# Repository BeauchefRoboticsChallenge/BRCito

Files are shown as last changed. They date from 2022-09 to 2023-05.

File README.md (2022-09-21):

# BRCito 2022

[][cc-by-nc-sa]

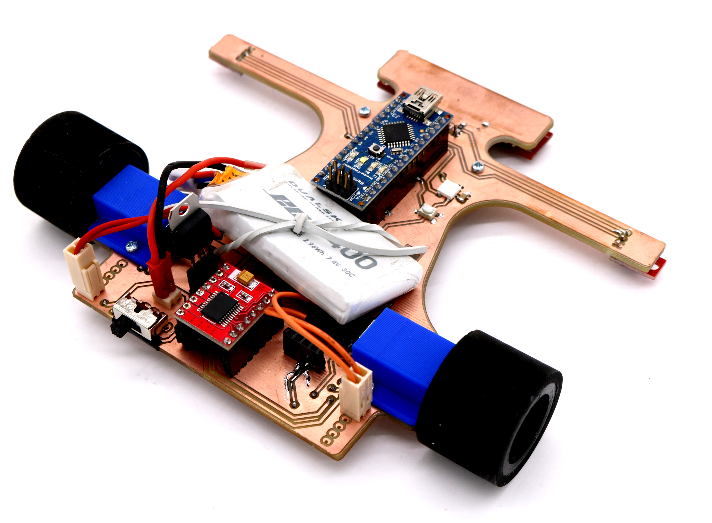
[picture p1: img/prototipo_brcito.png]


Robot velocista sigue-líneas desarrollado para BRC 2022.

El objetivo de este robot es servir de referencia y plataforma para apoyar la formación de los competidores. Está desarrollado en base a las tecnologías disponibles en un FabLab (impresión 3D, fresado de PCBs, Arduino) y comprende las componentes más básicas para funcionar de acuerdo a las reglas de la competencia.

Para poder entregar robots a los colegios participantes de la liga **Sub18** recibimos auspicio de [PCBWay](https://www.pcbway.com/) quienes nos otorgaron las placas electrónicas.

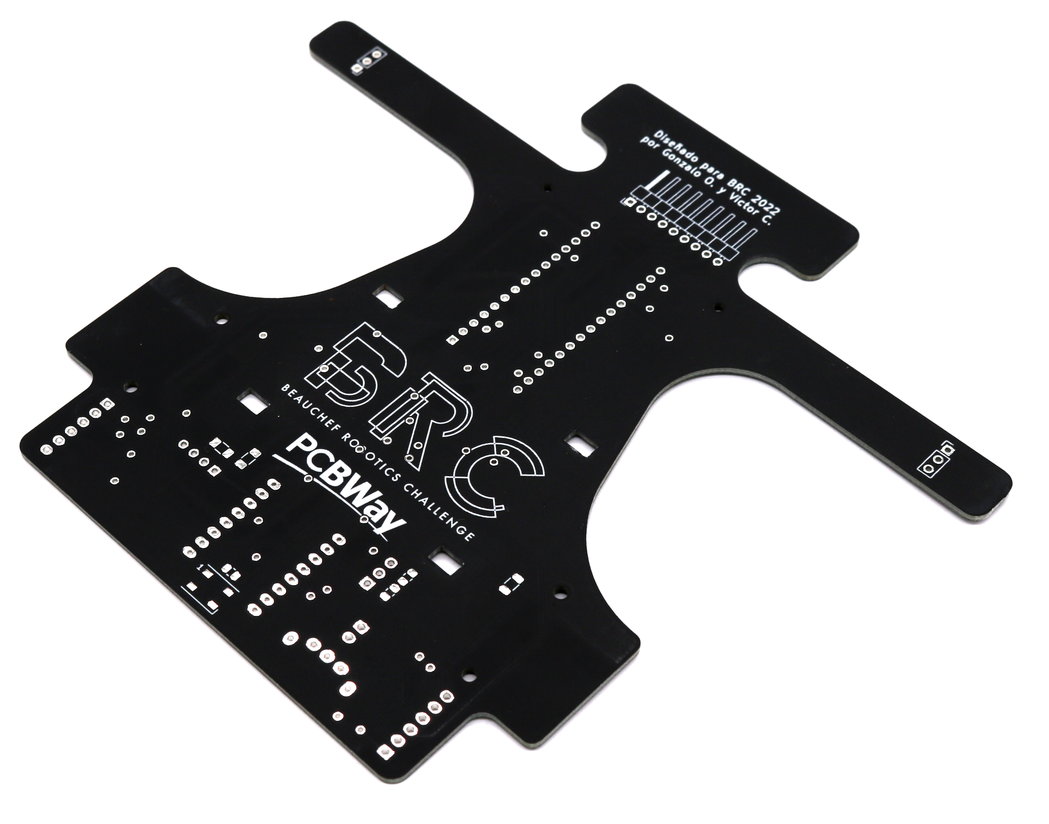
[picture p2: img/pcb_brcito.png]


## Diseño

### Antecedentes

Las funciones principales requeridas por el robot son:

- Distinguir una línea blanca en un fondo blanco
- Moverse lo más rápido posible, sin salirse de la pista

Para cumplir estas funciones, el robot requiere una construcción óptima en cuanto al tamaño/peso y las prestaciones de sus componentes que cumplirán estas funcionalidades. El diseño del robot puede seguir diferentes configuraciones (arreglos de sensores, motores, baterías, etc), dependiendo del tipo de control que se vaya a utilizar. Otras funciones secundarias corresponden a la interacción con el usuario (encender/apagar, activar, indicar acciones), así como cualquier otra que se desee agregar (como comunicación inalámbrica para el debugging).

En el contexto de la competencia, existirán marcadores a los costados del circuito que indicarán hitos como curvas, inicio y fin de la pista. También se fija el tamaño máximo como 25x25x20 centímetros (largo, ancho y alto) y que las ruedas no pueden contener elementos adherentes que dañen la pista.

### BRCito Negro PCBWay

El robot sigue líneas es controlador por un Arduino Nano. Las conexiones del Arduino con los sensores, necesarias para realizar su programación se pueden ver en la tabla

#### Pinout electrónico
| Pin Arduino | Descripción | Componente | Pin componente
| :--- | :--- | :--- | :-----  |
| A2 | Sensor Frontal 1 | Arreglo sensores QTR-8A | 6
| A3 | Sensor Frontal 2 | Arreglo sensores QTR-8A |5
| A4 | Sensor Frontal 3 | Arreglo sensores QTR-8A |4
| A5 | Sensor Frontal 4 | Arreglo sensores QTR-8A |3
| A6 | Sensor Frontal 5 | Arreglo sensores QTR-8A |2
| A7 | Sensor Frontal 6 | Arreglo sensores QTR-8A |1
| 6 | Rueda izquierda PWM | Driver motor TB6612FNG | PWMA
| 13 | Rueda izquierda A | Driver motor TB6612FNG  | AI1 |
| 10 | Rueda izquierda B | Driver motor TB6612FNG | AI2  |
| 5 | Rueda derecha PWM | Driver motor TB6612FNG | PWMB |
| 11 | Rueda derecha A | Driver motor TB6612FNG  | BI1 |
| 12 | Rueda derecha B | Driver motor TB6612FNG | BI2  |
| A1 | Sensor derecho | Sensor QTR-1A | out
| A0 | Sensor izquierdo | Sensor QTR-1A | out
| 9 | Leds RGB | Led RGB | din led
| 7 | Pulsador | Pulsador | pin pulsador

### Librerías de Kicad

En la carpeta [pcb/libs/](pcb/libs/) se encuentran las librerías de símbolos y footprints diseñados para los componentes que no existen en las librerías estandar de KiCad.

**Librería de símbolos**
* TB6612FNG_breakout

**Librería de footprints**
* QTR-8
* SPST Slide Switch (interruptor)
* TB6612FNG Breakout

## Librerías de Arduino

Para comunicarse con los leds WS2812b se puede utilizar la librería [Adafruit Neopixel](https://github.com/adafruit/Adafruit_NeoPixel).

Para los sensores infrarrojos QTR se puede utilizar la librería [QTR Sensors](https://github.com/pololu/qtr-sensors-arduino).

## Licencia
[][cc-by-nc-sa]

Este trabajo esta publicado bajo la licencia [Creative Commons Attribution-NonCommercial-ShareAlike 4.0 International
License][cc-by-nc-sa].

Si deseas utilizar nuestro robot en tus proyectos o si te interesa vender las placas, contáctanos y conversemos :)

[cc-by-nc-sa]: https://creativecommons.org/licenses/by-nc-sa/4.0/
[cc-by-nc-sa-image]: https://i.creativecommons.org/l/by-nc-sa/4.0/88x31.png
[cc-by-nc-sa-shield]: https://img.shields.io/badge/License-CC%20BY%20NC%20SA%204.0-lightgrey.svg

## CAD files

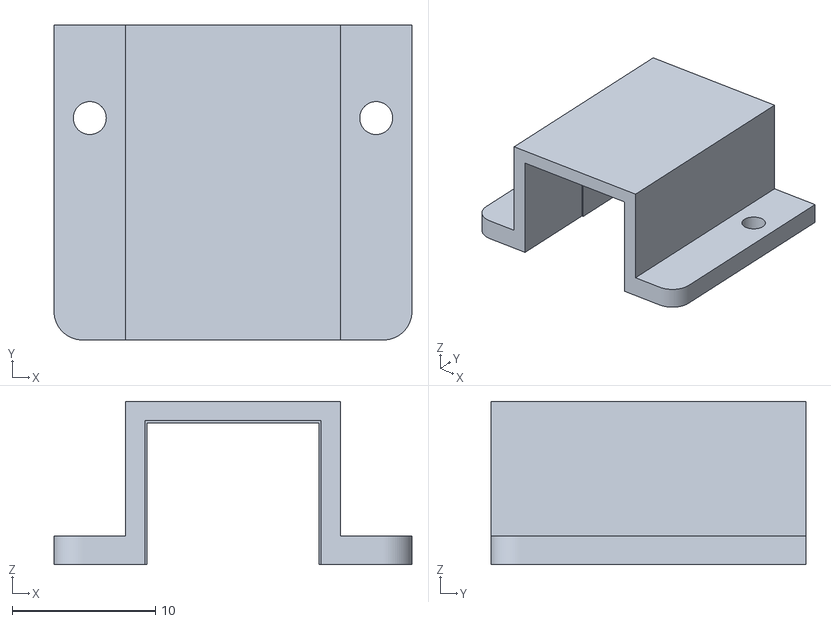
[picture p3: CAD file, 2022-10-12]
cad/BRCito_montaje_rueda.stl
25.0 x 22.0 x 11.4

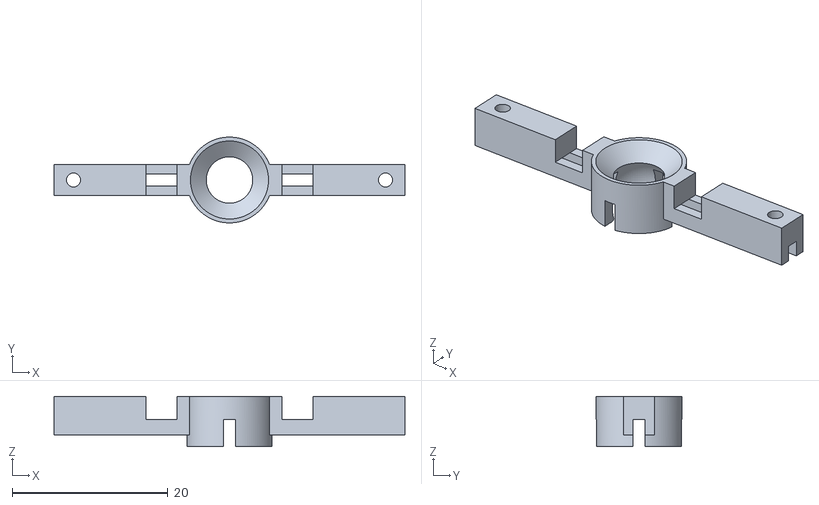
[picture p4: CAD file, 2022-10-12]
cad/BRCito_rueda_loca.stl
45.0 x 11.0 x 6.45

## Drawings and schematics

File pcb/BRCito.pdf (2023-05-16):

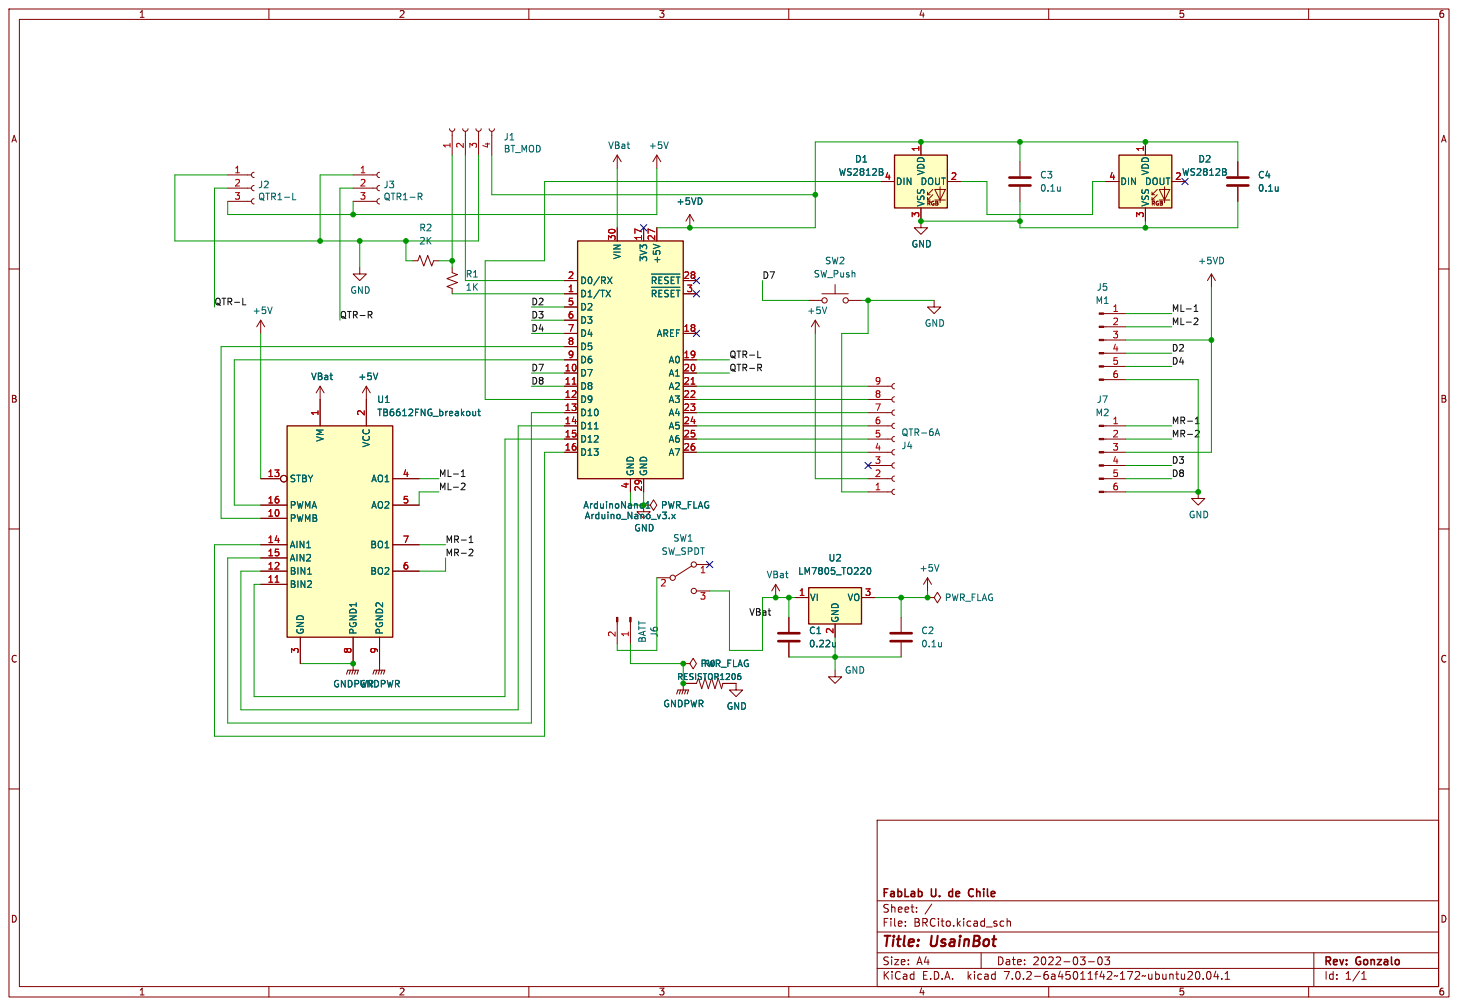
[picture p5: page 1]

1 PWMB 10 BIN2 11 BIN1 12 STBY 13 AIN1 14 AIN2 15 PWMA 16 VCC

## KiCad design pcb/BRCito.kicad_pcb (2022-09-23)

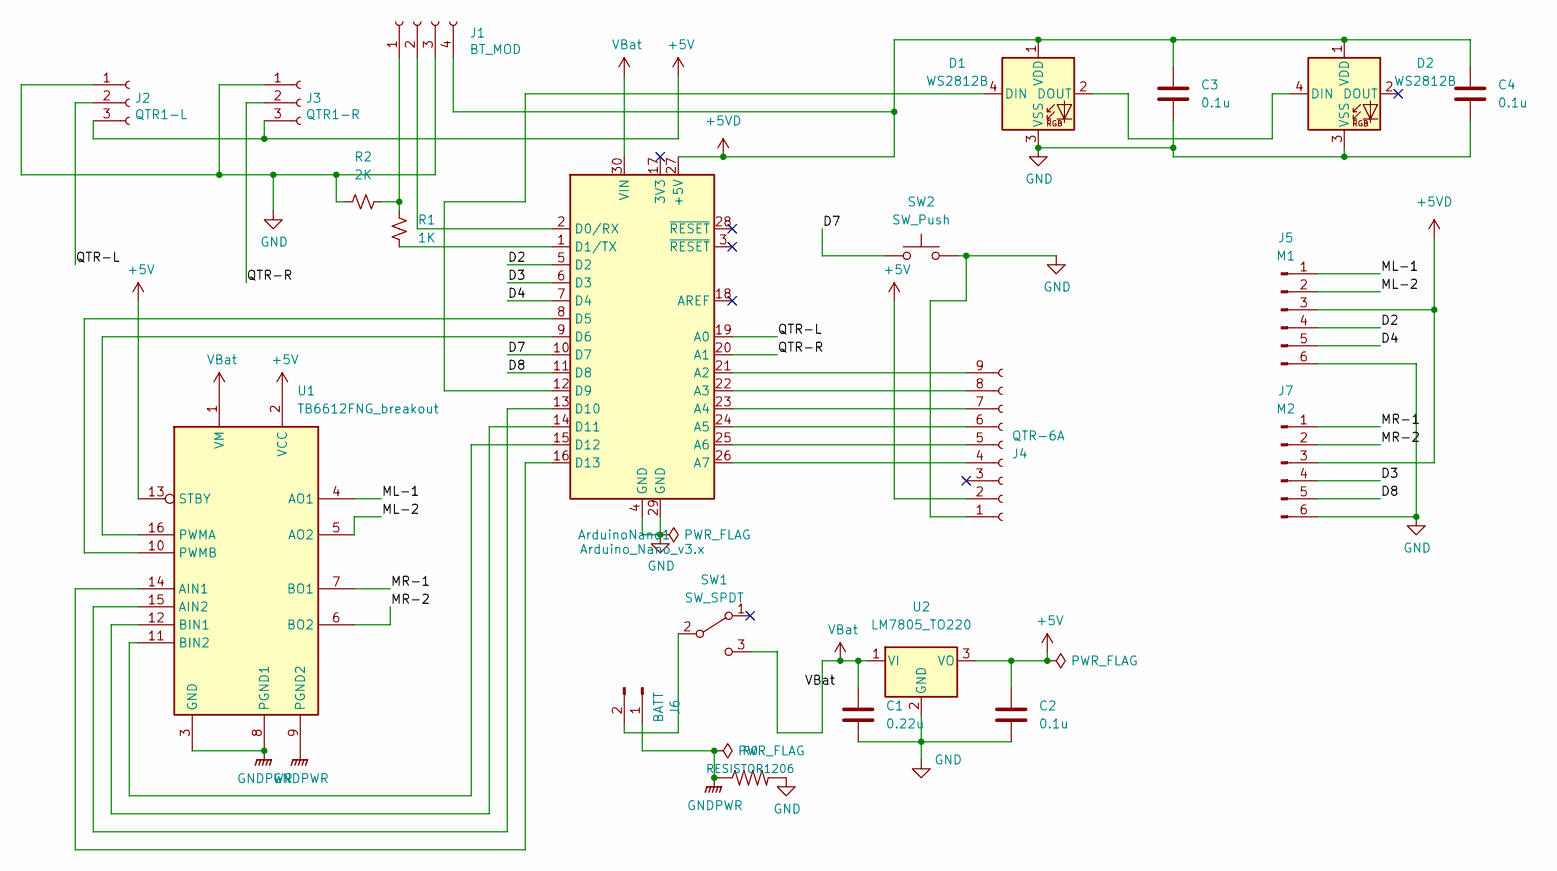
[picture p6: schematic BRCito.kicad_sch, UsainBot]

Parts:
ArduinoNano1: Arduino_Nano_v3.x; Arduino_Nano
C1: 0.22u; C_0805_2012Metric_Pad1.18x1.45mm_HandSolder
C2, C3, C4: 0.1u; C_0805_2012Metric_Pad1.18x1.45mm_HandSolder
D1, D2: WS2812B; LED_WS2812B_PLCC4_5.0x5.0mm_P3.2mm
J1: BT_MOD; PinSocket_1x04_P2.54mm_Vertical
J2: QTR1-L; PinHeader_1x03_P2.54mm_Vertical
J3: QTR1-R; PinHeader_1x03_P2.54mm_Vertical
J4: QTR-6A; PinHeader_1x09_P2.54mm_Horizontal
J5: M1; Molex_KK-254_AE-6410-06A_1x06_P2.54mm_Vertical
J6: BATT; Molex_KK-254_AE-6410-02A_1x02_P2.54mm_Vertical
J7: M2; Molex_KK-254_AE-6410-06A_1x06_P2.54mm_Vertical
R0: RESISTOR1206; R_1206_3216Metric
R1: 1K; R_1206_3216Metric_Pad1.30x1.75mm_HandSolder
R2: 2K; R_1206_3216Metric_Pad1.30x1.75mm_HandSolder
SW1: SW_SPDT; SPST slide switch
SW2: SW_Push; SW_Push_1P1T_NO_Vertical_Wuerth_434133025816
U1: TB6612FNG_breakout; TB6612FNG Breakout
U2: LM7805_TO220; TO-220-3_Vertical

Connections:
+5V: C2.1, J2.3, J3.3, J4.2, U1.2 (VCC), U1.13 (STBY), U2.3 (VO)
+5VD: ArduinoNano1.27 (+5V), C3.1, C4.1, D1.1 (VDD), D2.1 (VDD), J1.4, J5.3, J7.3
/D2: ArduinoNano1.5 (D2), J5.4
/D3: ArduinoNano1.6 (D3), J7.4
/D4: ArduinoNano1.7 (D4), J5.5
/D7: ArduinoNano1.10 (D7), SW2.1
/D8: ArduinoNano1.11 (D8), J7.5
/ML-1: J5.1, U1.4 (AO1)
/ML-2: J5.2, U1.5 (AO2)
/MR-1: J7.1, U1.7 (BO1)
/MR-2: J7.2, U1.6 (BO2)
/QTR-L: ArduinoNano1.19 (A0), J2.2
/QTR-R: ArduinoNano1.20 (A1), J3.2
GND: ArduinoNano1.4 (GND), ArduinoNano1.29 (GND), C1.2, C2.2, C3.2, C4.2, D1.3 (VSS), D2.3 (VSS), J1.3, J2.1, J3.1, J4.1, J5.6, J7.6, R0.2, R2.2, SW2.2, U2.2 (GND)
GNDPWR: J6.1, R0.1, U1.3 (GND), U1.8 (PGND1), U1.9 (PGND2)
unnamed: ArduinoNano1.1 (D1/TX), R1.2
unnamed: ArduinoNano1.2 (D0/RX), J1.2
unnamed: ArduinoNano1.8 (D5), U1.10 (PWMB)
unnamed: ArduinoNano1.9 (D6), U1.16 (PWMA)
unnamed: ArduinoNano1.12 (D9), D1.4 (DIN)
unnamed: ArduinoNano1.13 (D10), U1.15 (AIN2)
unnamed: ArduinoNano1.14 (D11), U1.12 (BIN1)
unnamed: ArduinoNano1.15 (D12), U1.11 (BIN2)
unnamed: ArduinoNano1.16 (D13), U1.14 (AIN1)
unnamed: ArduinoNano1.21 (A2), J4.9
unnamed: ArduinoNano1.22 (A3), J4.8
unnamed: ArduinoNano1.23 (A4), J4.7
unnamed: ArduinoNano1.24 (A5), J4.6
unnamed: ArduinoNano1.25 (A6), J4.5
unnamed: ArduinoNano1.26 (A7), J4.4
unnamed: D1.2 (DOUT), D2.4 (DIN)
unnamed: J1.1, R1.1, R2.1
unnamed: J6.2, SW1.2 (B)
VCC: ArduinoNano1.30 (VIN), C1.1, SW1.3 (C), U1.1 (VM), U2.1 (VI)

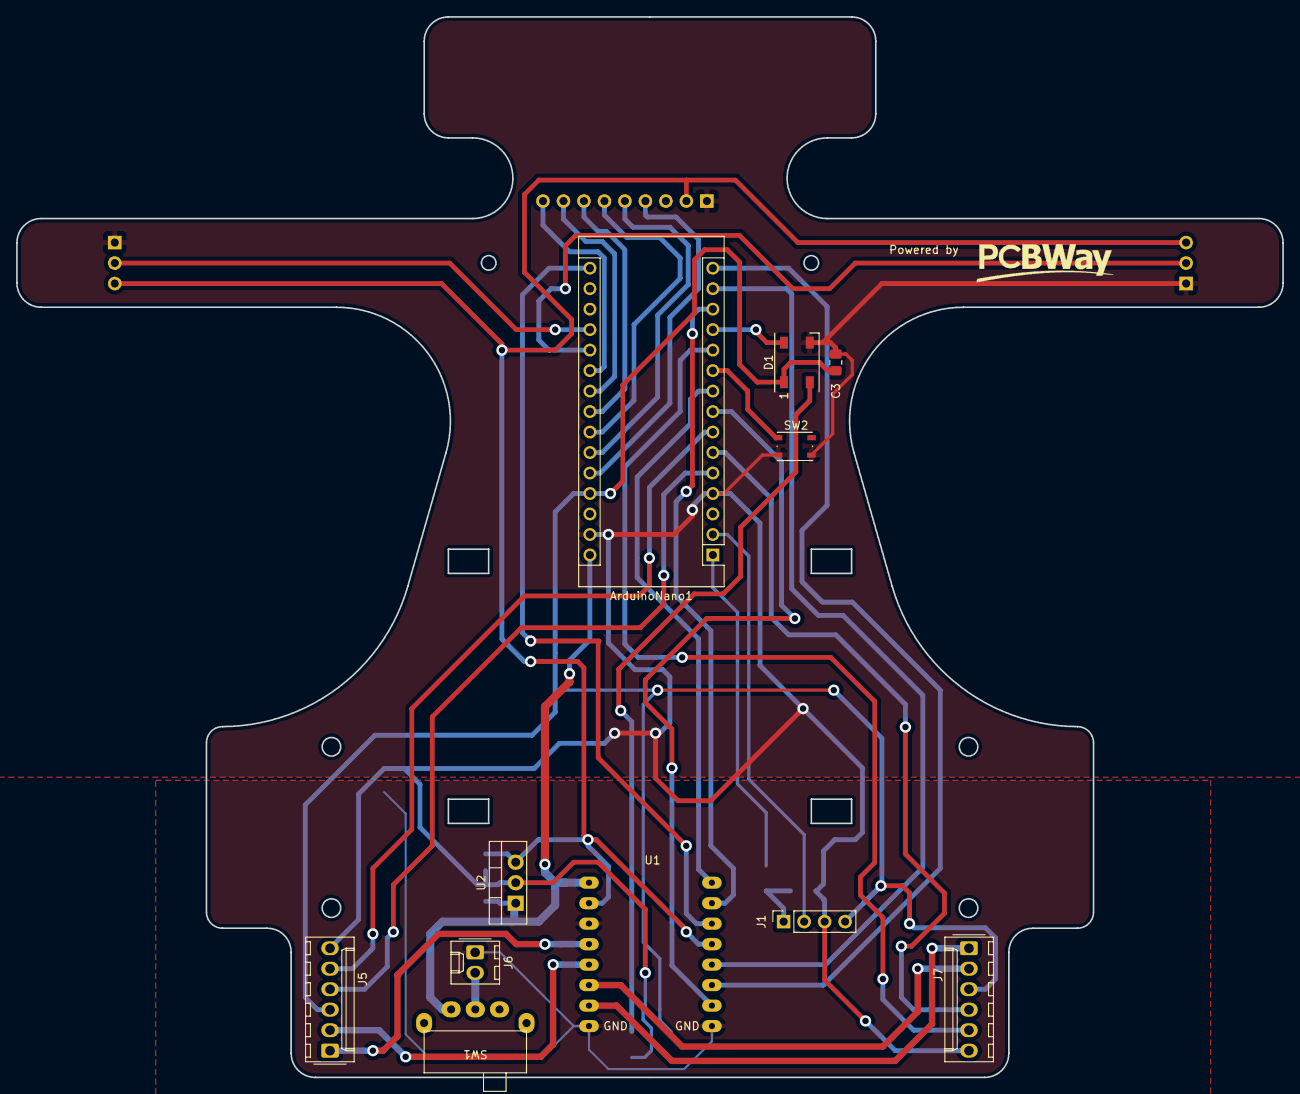
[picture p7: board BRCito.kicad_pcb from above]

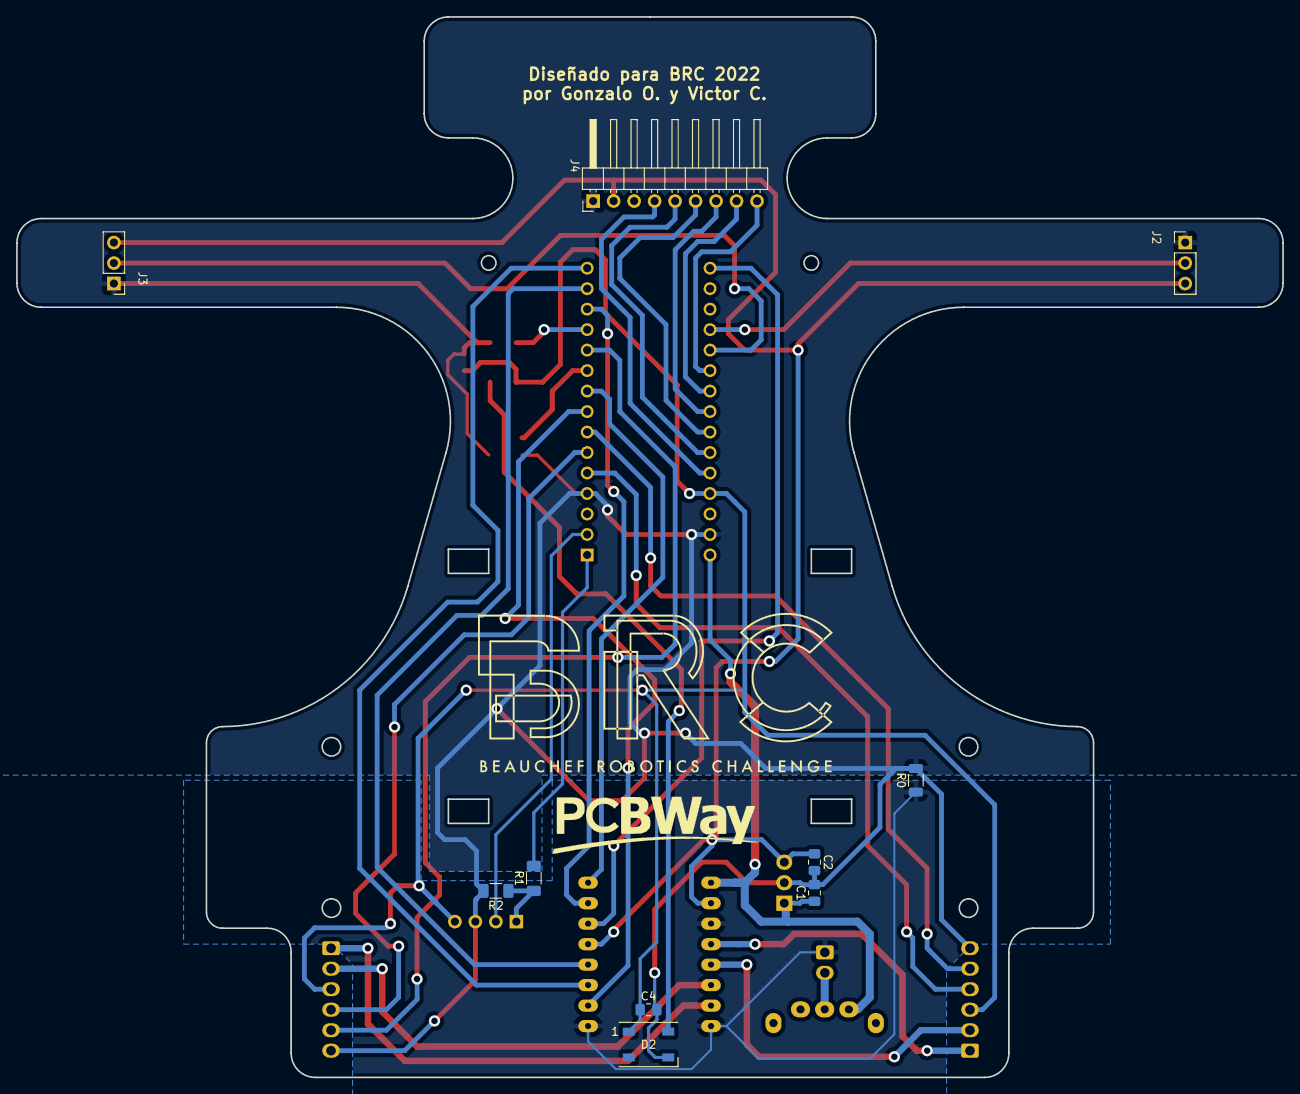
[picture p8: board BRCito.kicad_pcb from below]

Board: 2 copper layers, 157.0 x 131.5 mm, 21 parts (10 on the bottom side), 34 nets.

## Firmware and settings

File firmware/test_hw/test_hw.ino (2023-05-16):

#define DEBUG true


#include "DebugUtils.h"
#include <Adafruit_NeoPixel.h>
#include <QTRSensors.h>

#define LED_PIN 9
#define BUTTON_PIN 7
#define QTR_R 3
#define QTR_L 2

#define ML_IN1 13
#define ML_IN2 10
#define MR_IN1 11
#define MR_IN2 12
#define ML_PWM 6
#define MR_PWM 5

#define MD_STDBY 4


Adafruit_NeoPixel pixel = Adafruit_NeoPixel(1,LED_PIN,NEO_GRB+NEO_KHZ800);
QTRSensors qtr;

const uint8_t SensorCount = 8;
uint16_t sensorValues[SensorCount];

void setup() {
  // serial
  Serial.begin(115200);
  // led
  pixel.begin();
  // boton
  pinMode(BUTTON_PIN, INPUT_PULLUP);
  // sensores
  qtr.setTypeAnalog();
  qtr.setSensorPins((const uint8_t[]){A0,A1,A2,A3,A4,A5,A6,A7}, 8);

  // motores
  pinMode(ML_IN1,OUTPUT);
  pinMode(ML_IN2,OUTPUT);
  pinMode(MR_IN1,OUTPUT);
  pinMode(MR_IN2,OUTPUT);
  pinMode(ML_PWM,OUTPUT);
  pinMode(MR_PWM,OUTPUT);
  pinMode(MD_STDBY,OUTPUT);
}

void loop() {
  testButton();
  //testLed();
  //testSensors();
  //testMotors();

  //delay(50);
}

void testMotors(){
  int boton = digitalRead(BUTTON_PIN);

  digitalWrite(ML_IN1,HIGH);
  digitalWrite(ML_IN2,LOW);
  digitalWrite(MR_IN1,LOW);
  digitalWrite(MR_IN2,HIGH);

  if(boton == 0){
    digitalWrite(MD_STDBY,HIGH);
  }
  else {
    digitalWrite(MD_STDBY,LOW);
  }
  analogWrite(ML_PWM,255);
  analogWrite(MR_PWM,255);

  delay(100);

}

void testButton(){

  int boton = digitalRead(BUTTON_PIN);
  DEBUG_PRINTLN(boton);

}

void testLed(){

/*
  uint32_t color = pixel.Color(255,0,255); // magenta
  pixel.setPixelColor(0,color);
  pixel.show();
*/
  PlasmaPulse(30);

}


void testSensors(){
  // read raw sensor values
  qtr.read(sensorValues);

  for (uint8_t i = 0; i < SensorCount; i++)
  {
    Serial.print(sensorValues[i]);
    Serial.print('\t');
  }
  Serial.println();

  delay(100);

}

void PlasmaPulse(uint8_t wait) {
  uint16_t i, j;
  uint8_t brightness = 10;

  for(i=0; i<pixel.numPixels(); i++) {
    pixel.setPixelColor(i, pixel.Color(255, 255, 255));
  }
  pixel.show();
  delay(wait);
  //Adjust 60 and 90 to the starting and ending colors you want to fade between.
  for(j=170; j>=135; --j) {
    for(i=0; i<pixel.numPixels(); i++) {
      pixel.setPixelColor(i, Wheel((i+j) & 255));
    }
    pixel.show();
    brightness -= 6;
    pixel.setBrightness(brightness);
    delay(wait);
  }

  for(j=135; j<1170; j++) {
    for(i=0; i<pixel.numPixels(); i++) {
      pixel.setPixelColor(i, Wheel((i+j) & 255));
    }
    pixel.show();
    brightness += 6;
    pixel.setBrightness(brightness);
    delay(wait);
  }

  for(i=0; i<pixel.numPixels(); i++) {
    pixel.setPixelColor(i, pixel.Color(255, 255, 255));
  }
  pixel.show();
  delay(wait);

}

// Input a value 0 to 255 to get a color value.
// The colours are a transition r - g - b - back to r.
uint32_t Wheel(byte WheelPos) {
  if(WheelPos < 85) {
   return pixel.Color(WheelPos * 3, 255 - WheelPos * 3, 0);
  } else if(WheelPos < 170) {
   WheelPos -= 85;
   return pixel.Color(255 - WheelPos * 3, 0, WheelPos * 3);
  } else {
   WheelPos -= 170;
   return pixel.Color(0, WheelPos * 3, 255 - WheelPos * 3);
  }
}

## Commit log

2022-08-06 firmware de prueba hw y placa
    [usainbot2.kicad_pcb, usainbot2.kicad_sch]
2022-09-07 added kicad libraries with switch and tb6612fn
2022-09-21 actualiza el Readme con información de las librerías de kicad
2022-09-23 corrige error de diseño
    [usainbot2.kicad_pcb, usainbot2.kicad_sch]
2022-10-12 se agregan piezas 3d en stl
    [BRCito_montaje_rueda.stl, BRCito_rueda_loca.stl]
2023-05-16 update files
    [BRCito.kicad_pcb, BRCito.kicad_sch, usainbot2.kicad_pcb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]

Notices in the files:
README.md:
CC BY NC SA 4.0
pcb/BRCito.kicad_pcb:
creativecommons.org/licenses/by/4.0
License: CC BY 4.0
